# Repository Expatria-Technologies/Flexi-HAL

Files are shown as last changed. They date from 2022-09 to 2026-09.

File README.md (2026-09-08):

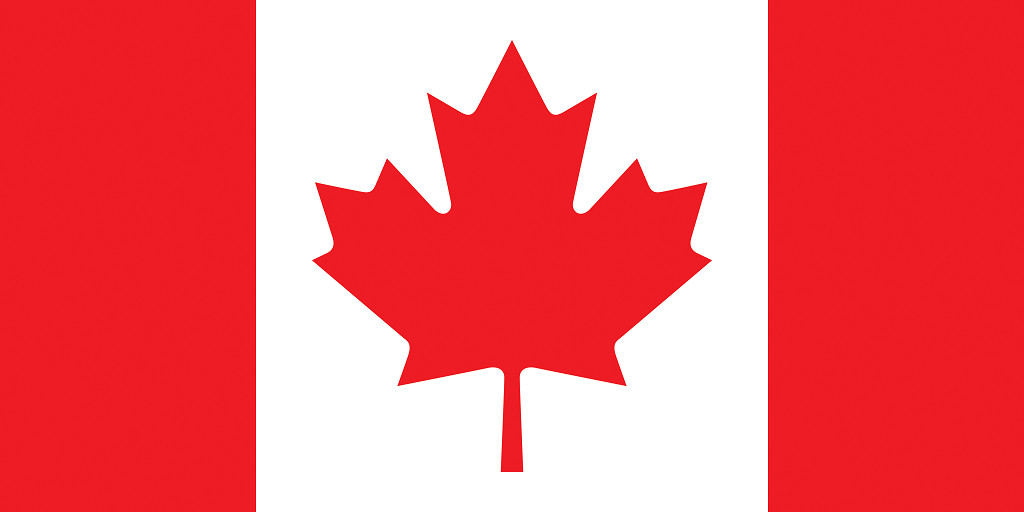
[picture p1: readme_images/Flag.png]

### Canadian-designed open source hardware. For everyone.

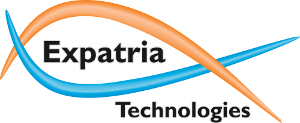
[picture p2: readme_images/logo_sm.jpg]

# Flexi-HAL CNC Controller
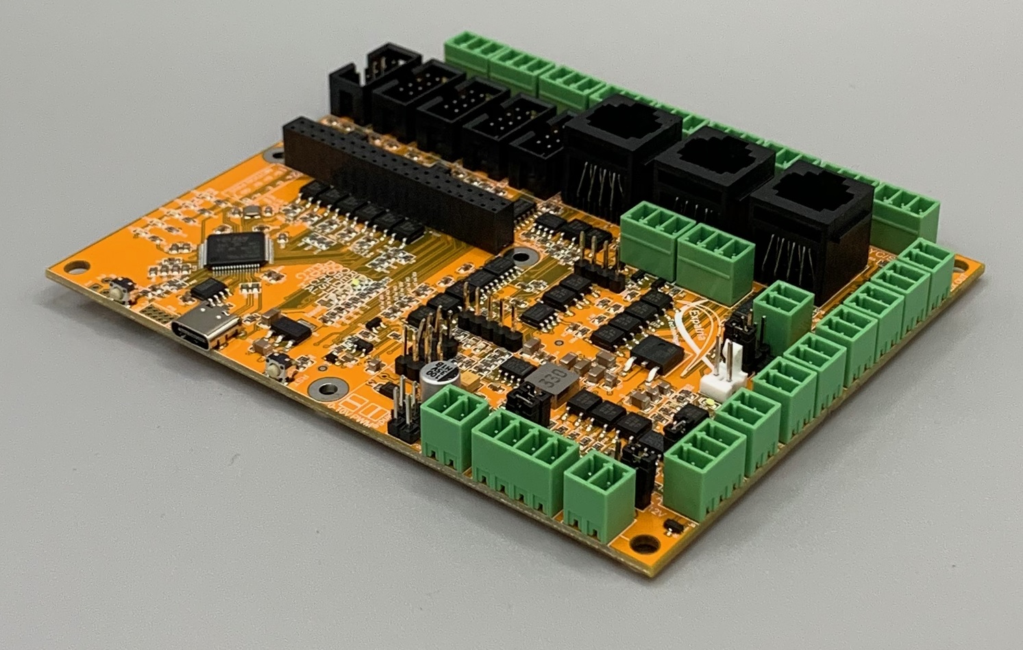
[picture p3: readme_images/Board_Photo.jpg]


Expatria Technologies GRBLHAL and LinuxCNC (and more!) CNC control board

Currently available in our online store:

https://expatria.myshopify.com/products/flexi-hal

Please consider buying a board to support our open-source designs. 

The Flexi-HAL was designed to be an EMI resistant IO platform for any microcontroller based CNC/motion control firmware or software.  This board includes a few features that we couldn't find on other boards, and it reduces the amount of extra wiring in our setups.  In the co-operative spirit of the PrintNC and other CNC communities, and Open Source Hardware, the Flexi-HAL will be licensed and free to use by all parties, including commercial parties, under the CERN-OHL-S V2 license.  It is our hope that the community finds the design useful and that it may be carried forward to help advance the PrintNC and broader CNC hobby community.

The Flexi-HAL incorporates community driven elements from the PrintNC Electronic Standardization (EST) Project.  As part of this project, two additional breakout boards have been created for the user controls and limits/probe inputs.  These are simple boards and could easily be milled and hand assembled, but fabrication files for each are available in the CAM_Outputs folder.  The inputs are accessible via the RJ45 connectors on the Flexi-HAL mainboard.  In addition, the Flexi-HAL is intended to be used with the Expatria Real-Time jog controller or similar peripheral:

https://github.com/Expatria-Technologies/RT_Jog_Controller

The key features of the Flexi-HAL:

1) 5 Axis of isolated step/dir motor control featuring high-speed digital isolators and differential signal drivers for maximum signal integrity and step rates.
2) Integrated support for 3 wire inductive type powered switches.
3) Onboard 5V power regulator.
4) Integrated RS485 with automatic direction control.
5) Support for closed loop stepper motors and servos with alarm feedback.
6) Differential interface for a spindle encoder inputC.
7) Real-time control port for remote handwheels and pendants.
8) Raspberry Pi GPIO connector allows integration of sender software and allows the board to host a full LinuxCNC installation.
9) 10V or 5V spindle control including PWM output via selectable jumpers.
10) 3 wire (powered) connections for standard CNC buttons on a breakout RJ45 connector that utilizes components compatible with the PrintNC EST project.
11) XYZA limit switches and probe/toolsetter on breakout RJ45 connector.
12) Flood/Mist/Spindle relay drivers.
13) Additional auxilliary inputs and relay driver outputs.
14) All machine facing IO is galvanically isolated from the MCU and user interfaces.
15) Easy reliable USB-C connection to a PC
16) GRBLHAL Ethernet Websockets or Telnet communication options with uFlexiNET module.
17) GRBLHAL SD card G-Code streaming and macro/subroutine storage (including looping and conditional execution) with uFelxiNET module.

Pre-compiled GRBLHAL binaries from are located here:  
https://github.com/Expatria-Technologies/STM32F4xx/releases

Source code for the customized Remora component to run in LinuxCNC is located here:  
https://github.com/Expatria-Technologies/remora-flexi-hal

Prebuilt Raspberry Pi 4B image is located here:  
https://github.com/Expatria-Technologies/Flexi-Pi

Accessory Breakout PCBs are located here:  
https://github.com/Expatria-Technologies/EST_Accessory_PCB

Various community mods and accessories are located here:  
https://github.com/Expatria-Technologies/Mods-Accessories

Recommended GRBLHAL Post Processor is here:  
https://github.com/Dietz0r/grblHAL_Fusion360_Post_Processor

uFlexiNET expansion card is here:  
https://github.com/Expatria-Technologies/uFlexiNET

The uf2 bootloader can be found here:  
https://github.com/Expatria-Technologies/tinyuf2/releases

## Flexi-HAL Overview

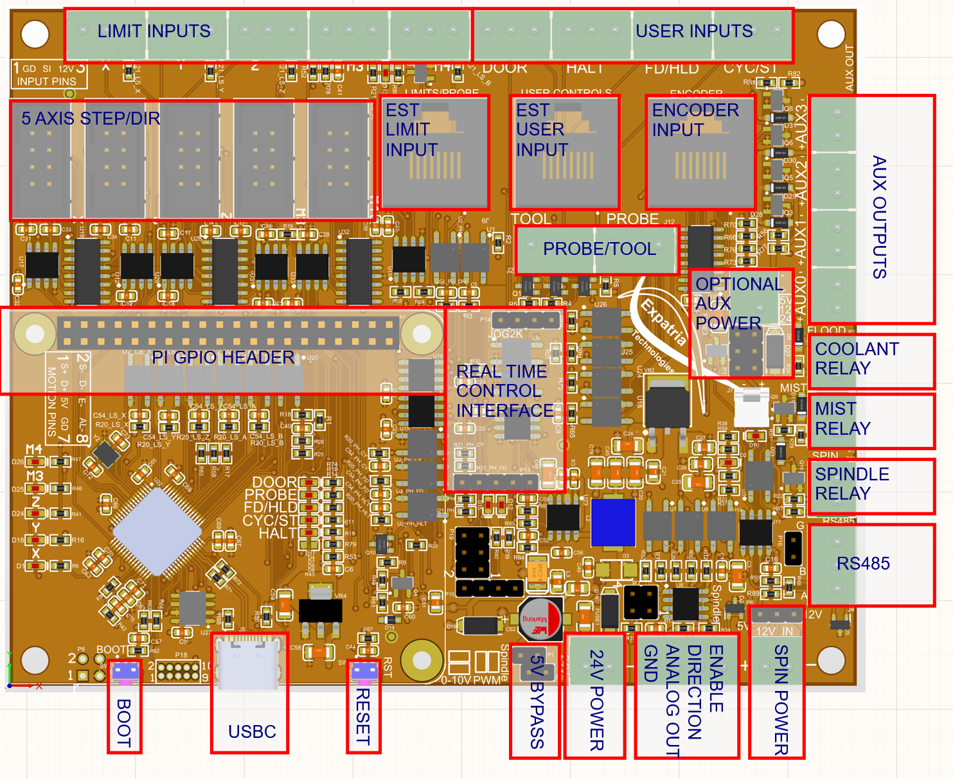
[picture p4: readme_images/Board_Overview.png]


Bottom side pin labels:

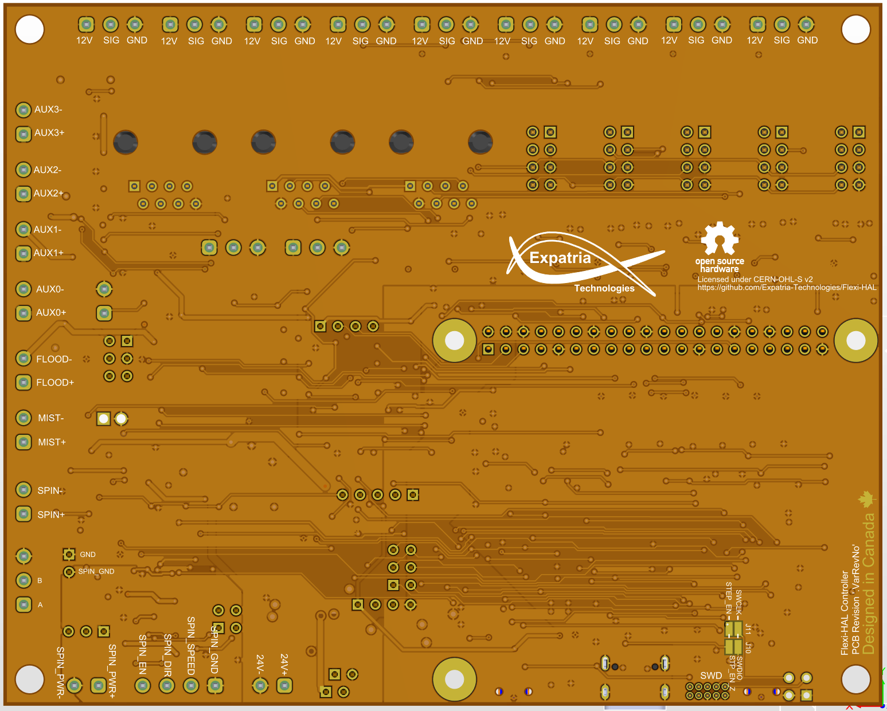
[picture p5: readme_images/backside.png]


Pinout List:

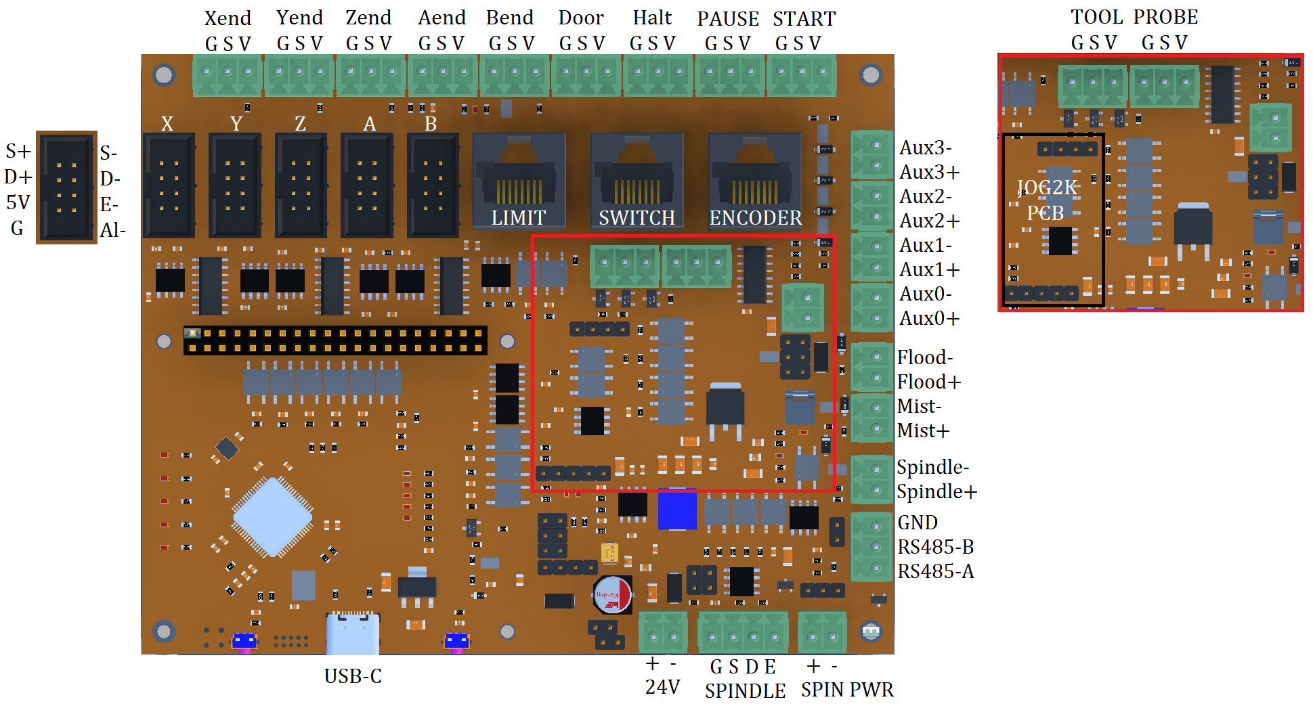
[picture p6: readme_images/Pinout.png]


### STM32F446 Microcontroller

Primarily, the board supports both GRBLHAL and LinuxCNC.  Binary firmware builds for different axis configurations are published on the Expatria Github.  In addition, a customized port of the awesome Remora project has been developed alongside Flexi-HAL so that you can easily switch to LinuxCNC.  With LinuxCNC, a Raspberry Pi 4b is installed in the Pi GPIO header to ensure the best possible signal integrity for the SPI step generation interface.

By using a common STM32F4 MCU, the Flexi-HAL is also able to easily host ports of uCNC, Marlin and even Klipper so it can drive much more than just CNC machines.

### UF2 Bootloader
The Flexi-HAL is meant to be used with a UF2 bootloader. All boards from Expatria will come with this bootloader installed. This allows you to upgrade or change the firmware on the flexi as easily as copying a file to a USB drive.  Pre-built binary firmwares from Expatria are distributed as UF2 files.  There are two ways to access bootloader mode and change the firmware:
1) Power up the MCU section (connect the USB cable) while holding the CYC/ST and FD/HLD buttons.
2) Double-tap the reset (RST) button on the side of the board near the USBC port.

Once in bootloader mode, the Flexi will appear as a USB storage device called "FLEXI446" and the X limit light will flash briefly if there is no signal asserted on that pin (switch is open).  Simply copy the new firwmare to this USB drive and the board will automatically install it and reboot.  Some operating systems may give an error when flashing is complete because the 'disk' was removed without ejecting it.  This error can be ignored.

### Power Input
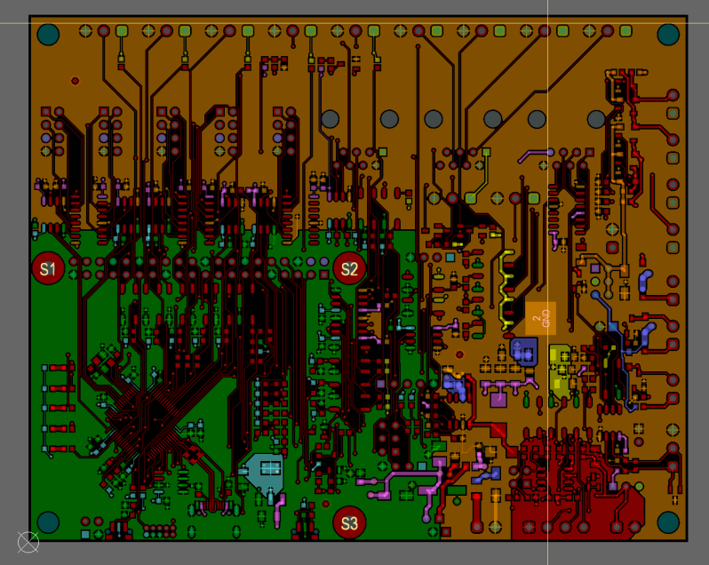
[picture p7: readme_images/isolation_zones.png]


The Flexi-HAL features the capability for full power and ground isolation between the sensitive microncontroller and host circuits, and the external IO that extends out to the rest of the machine.  There is a single input for 12-24VDC.  The board has its own onboard 5V regulator to power the stepper drivers and external RS485 interface.  There is also a small capacity 12V LDO that is specifically for driving the limit and user switches, as well as optionally providing the base voltage for the 10V spindle output.

Flexi-HAL has reverse polarity as well as over-current protection beyond 1A.  This is important to consider when using external relays that draw a lot of current as this may overwhelm the capacity of the board.  If you need to drive more than 250 mA through the auxillary and mist/coolant relay outputs, external relays are likely required.

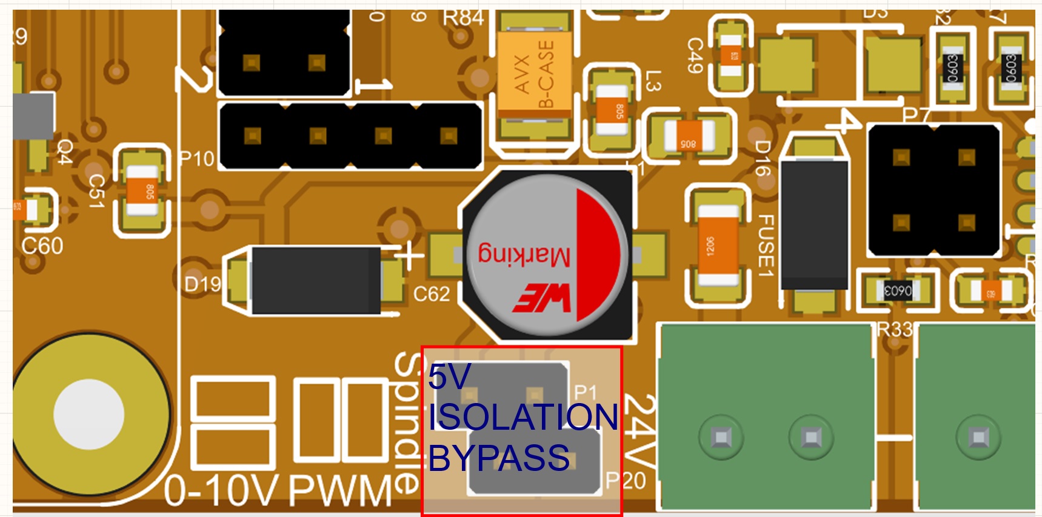
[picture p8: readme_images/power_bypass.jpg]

Normally the MCU and RPI header will be powered via the USBC connector.  The Jog2K is also powered from the isolated domain.  By installing two jumpers on the above offset pins, the 5V power and ground isolation can be bypassed and the Flexi-HAL will operate without an external 5V supply in a semi-isolated state.  This does reduce the EMI resistance of the board and is not recommended when sending Gcode via the USBC connector.

Note: With the isolation jumpers not-populatd, and the Flexi-HAL connected to 12-24v power, it may appear that the board is ready to run as some LEDs illuminate. You MUST provide 5v power to the isolated domain (MCU, Jogger) either through USB or the bypass jumpers in order for the MCU and Jogger to turn on!

### Stepper Drivers
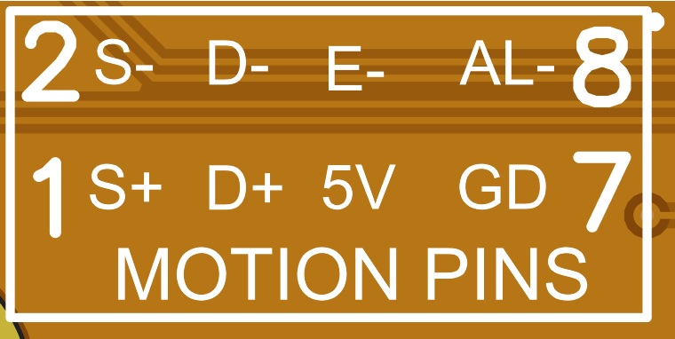
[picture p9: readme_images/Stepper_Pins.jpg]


The stepper drivers are designed to be used with IDC connectors that are quick to assemble.  Unfortunately you will need to ensure that at the external driver the high and low signal pairs are connected correctly as there is no standard pinout on these drivers.  The 8 pin connection allows you to run a high and low pair for every signal to ensure the best possible signal integrity.  The Flexi-HAL uses high speed digital isolators and differential RS-422 style signal drivers for the motion signals.

When using the alarm input the external drivers need to be configured for open-drain, active-low output.  The alarm output must be high impedance during normal operation.  In normal operation the blue MOTOR LED will be lit indicating that there are no active alarms.

Typical wiring for most open-loop stepper drivers: 



### Analog Spindle Control

Traditional GRBL spindle control interface for 0-10V or 0-5V spindle control.  Uses a dual-stage output driver for linear response.  Spindle power supply is selectable between 5V, 12V or external.  Note that when running the board with less than 14v input, it may not be possible to reach the full 10V output level - this is due to the dropout of the 12V LDO.  In this case, use the external spindle power input to connect your 12v and bypass the LDO for the spindle control voltage.

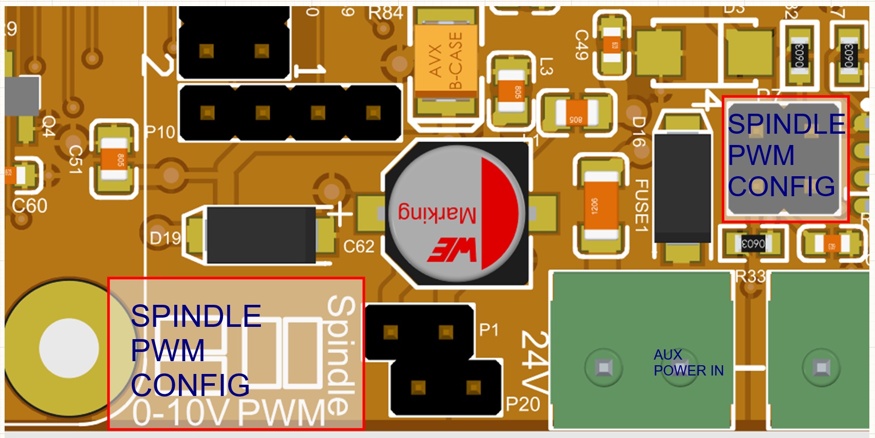
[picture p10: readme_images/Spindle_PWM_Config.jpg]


Near the main power input of the Flexi-HAL there is a diagram showing how a set of jumpers may be configured to enable 0-10V analog or TTL PWM output.  This jumper allows you to have a 12V compliant TTL PWM signal to drive a device like a laser engraver or an ESC.

Two headers - 3 pin P6 and 2 pin P16, connect the analog spindle section to the rest of the board.  P6 allows you to power the spindle section from either the onboard 5V or 12V rails.  If you remove P6 and P16 then the spindle section is completely isolated from the rest of the system and in this configuration can be used to drive motor controllers that require a floating control voltage.  Also, when driving the board with less than 14V input, it may not be possible to adjust the spindle output voltage to the full 10V.  In this case we recommend removing P6 (leave P16 in place) and applying 12V to the external spindle supply input directly.

### RS485 Spindle Control
This interface is primarily intended to be used with a Huanyang style VFD for spindle control.  The A, B and G (common) pins are marked on the top and bottoms sides of the PCB.  Simply connect the appropriate pins to the terminals on the VFD.  Note that the G pin should be used for signal common, it should not be connected to the shield of a shielded cable.

https://github.com/grblHAL/Plugins_spindle/

### 5 Axis limit inputs

By default both GRBL and the Flexi-HAL expect NPN NC limit switches.  PNP switches are not supported. NO switches can also be used on any switch input.

The first four axes have single limit inputs that are also accessible via the RJ45 EST limit breakout connector.  GRBL always knows the direction of travel so individual min and max pins are not required.  Auto-squaring is supported by enabling ganged axes in GRBLHAL and setting the appropriate pins.

In addition to the limit signals, there are two probe input pins on the limit RJ45 breakout connector and the main PCB that are multiplexed via XOR logic and share a single input pin on the microcontroller.

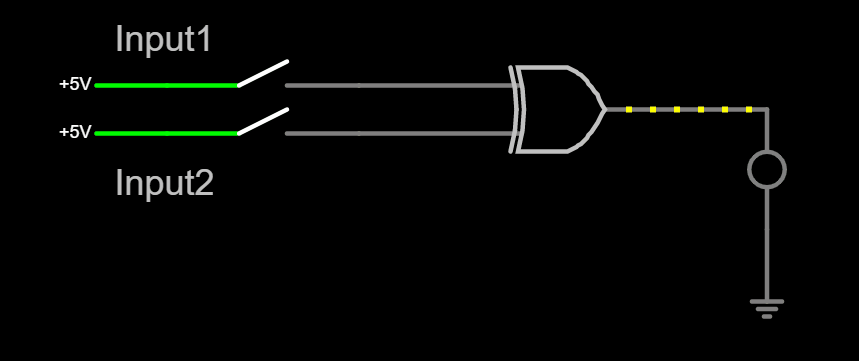
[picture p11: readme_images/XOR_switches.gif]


For the dual-input signals there is no need to terminate unused ports.

The RJ45 pinout:

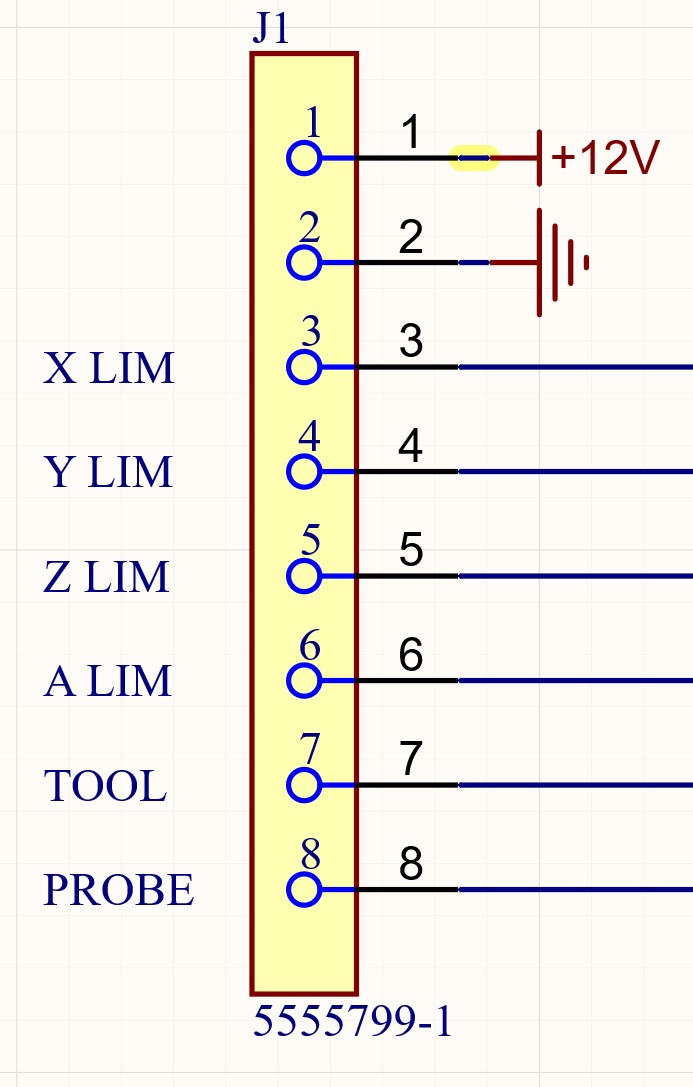
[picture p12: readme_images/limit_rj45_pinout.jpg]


### User Buttons

Standard CNC functions are mapped to 4 inputs.  These signals are primarily intended to be used via the user RJ45 connector.  They are also exposed via 3 wire connections on the main PCB.  These inputs have the same circuitry as the limit inputs and are NPN.  Connect SIG and GND to assert the signal.  When multiplexed these signals must be NO logic.

The RJ45 pinout:

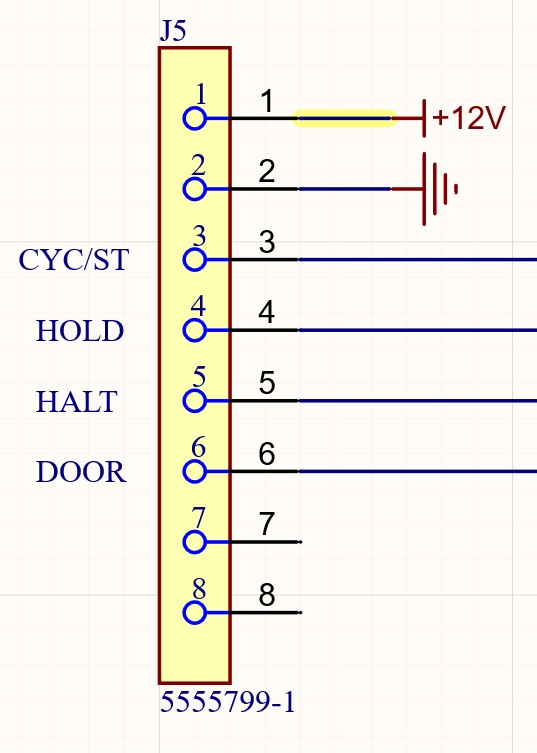
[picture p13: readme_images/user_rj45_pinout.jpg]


The HALT signal is not a safety feature and should not be used in place of a true electrical emergency stop.  It is intended to notify the controller of urgent requests and should be NO as it is shared between the PCB terminal block, RJ45 output and motor alarm.

### HALT Polarity Selection

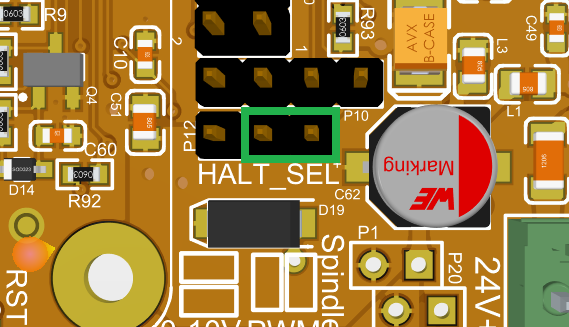
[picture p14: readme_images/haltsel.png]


Starting from A5 revision, the HALT signals from the Flexi-HAL board header port and the RJ45 user button breakout port are connected via an XOR gate. 
This was added to allow mixing "Normally Closed" (NC) and "Normally Open" (NO) switches.

At the default jumper position (illustrated above), Halt is triggered if the two ports have __different__ signals (High vs Low).
This means that a single NO, 2 NO, or 2 NC switches can be used.

| | Engaged Switch | Other Switch |
|---|---|---|
|Single NO | High | Low (Unconnected)|
|Two NO | High | Low |
|Two NC | Low | High |

If you wish to mix NO and NC, you need to move the jumper. Then Halt triggers if the two ports have __same__ signals.
Examples of this is using both the User Button Breakout (NO) and the common Toolsetter with overtravel protection (NC).
| | Halt button (NO)| Toolsetter overtravel (NC)|
|---|---|---|
|Halt pushed | High | High |
|Toolsetter pushed| Low | Low |

If you are in doubt of the correct header position for your case, you may simply try both positions and choose the one where the HALT signal is not asserted (red light is not on) when in the nominal operating condition.

(__Note:__ Do not change GRBL setting 14 to try and invert the halt("EStop"), as this is not the same and can make the Jog2K Halt button unresponsive)

### Spindle, Flood and Mist relay drivers
The Spindle, Flood and Mist relay outputs are driven from the main board supply.  External relays should be selected to match the power supplied to the Flexi-HAL.  The absolute maximum coil current for each output should not exceed 250mA.  In general, the coil resistance should be 150 Ohm or greater.  The relay outputs are active-low, the high side is connected to the main power input.

### Auxillary relay drivers
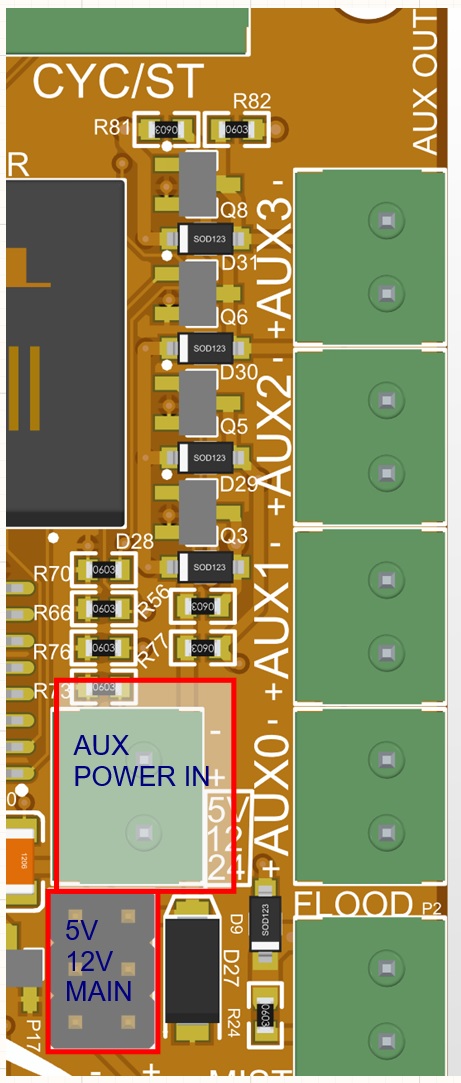
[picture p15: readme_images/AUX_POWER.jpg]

Four axilliary relay outputs are exposed.  These have a maximum combined drive current of 1000 mA when operated via a dedicated power supply.  The relay voltage can be selected via a 3 pin jumper between the main board power supply, the onboard 12V supply and the onboard 5V supply.  If the jumper is left unpopulated power for the aux outputs is supplied via the dedicated (fused and polarity protected) input.  The 12V and 5V options cannot drive more than 20 mA per pin and are only used for TTL signalling applications - they should never be used to drive inductive loads.  Never populate P17 and the external supply at the same time.  When driving external relays, the coil resistance should be 150 Ohm or greater.  The relay outputs are active-low, the high side is connected via the power selection jumper.

### Real-Time Control Port
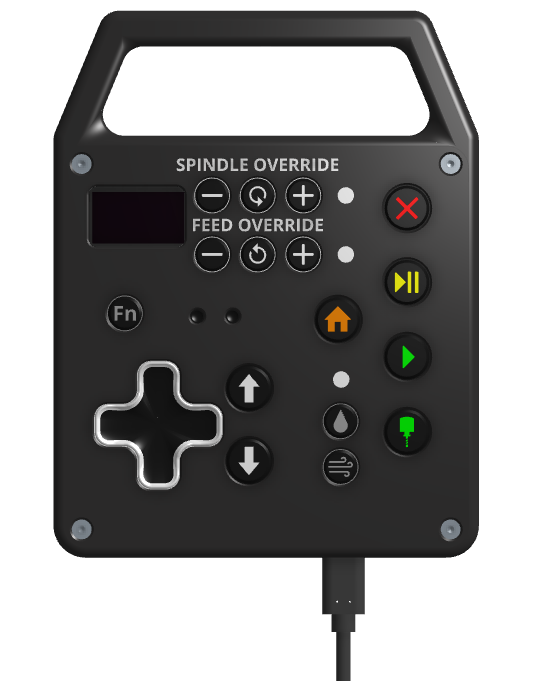
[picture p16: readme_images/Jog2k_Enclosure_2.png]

This port is intended to allow for external pendant type devices to issue real-time jogging and override controls to the motion  controller.  It uses I2C signalling and adds additional signals for the keypad interrupt as well as the Halt signal.  We feel that a robust and wired control is the safest way to interact with a CNC machine in real time.  A simple reference controller implementation is under active development, but there are some code examples referenced in the GRBLHAL I2C keypad plugin repository:

https://github.com/grblHAL/Plugin_I2C_keypad/

https://github.com/Expatria-Technologies/RT_Jog_Controller/

### Spindle Sync Port
This port allows a differential connection to an external module for a robust GRBLHAL lathe implementation or to support a high-speed encoder input for LinuxCNC.  An encoder such as E6B2-CWZ1X is suitable for most spindle applications.

There is also a small breakout available that exposes these signals for 5V single-ended NPN input to interface with more basic sensors and other switched inputs.

The RJ45 pinout:

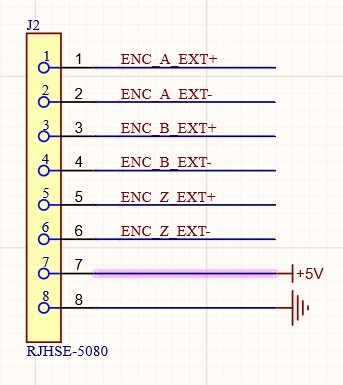
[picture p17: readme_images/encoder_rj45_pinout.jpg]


### Raspberry PI expansion header
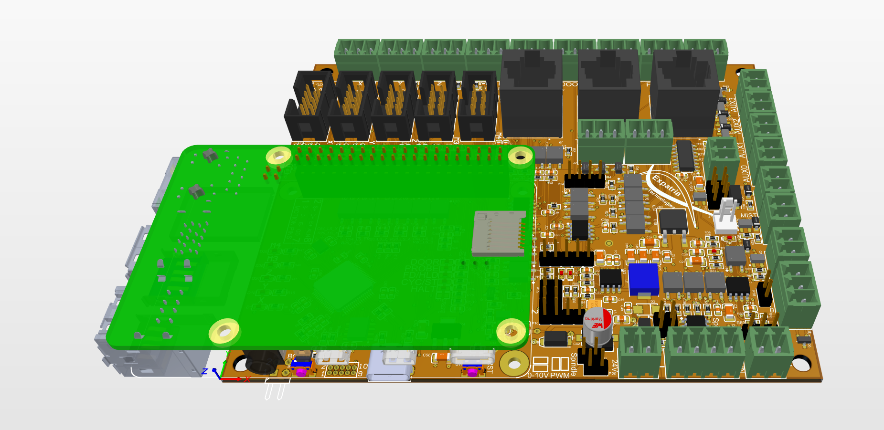
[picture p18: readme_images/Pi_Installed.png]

The Rasberry Pi GPIO header allows the Flexi-HAL to host a full Raspberry Pi type SBC.  This allows the platform to support LinuxCNC via the Remora project.

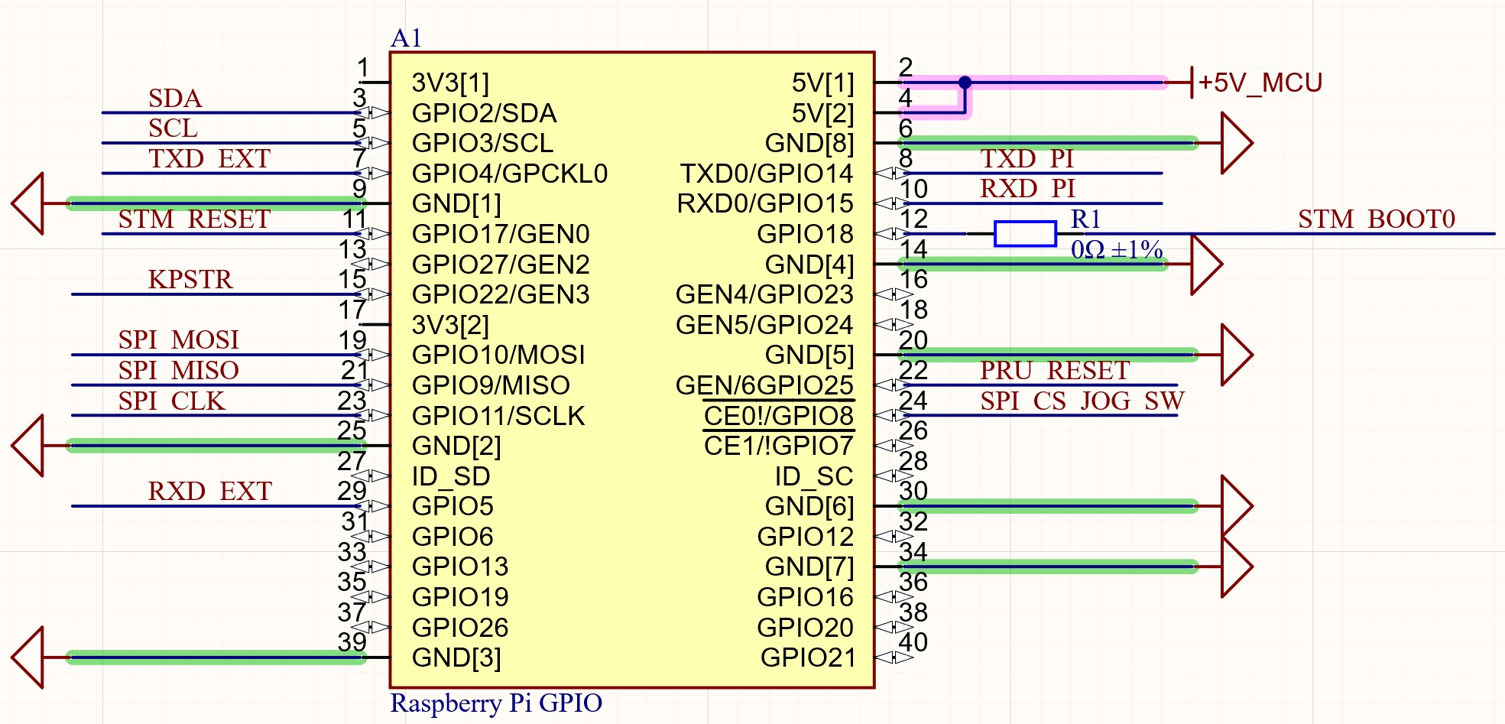
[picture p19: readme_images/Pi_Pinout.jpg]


### Accessories
Some 3D printed accessories are avilable in [Mods & Accessories](https://github.com/Expatria-Technologies/Mods-Accessories/), including a DIN rail mount and enclosures/mounts for the limit and button breakouts.

### Default Jumper Locations

By default the following jumpers (shown in the graphic in RED) should be populated.
This has the following effects:
The RPI Header uart is connected to the internal MCU UART - this is necessary to flash Remora firmware from the RPI and also is used with the uFlexiNET module for the SD card chip select.
The HALT polarity is set for use with an NO button like the button breakout.
The analog spindle output is set for 0-10V.
The analog spindle section is connected to the onboard 12V supply.
The analog spindle section ground is connected to the PCB external ground.
The aux outputs are powered via the main 24V input.

### Example Wiring Diagram
A comprehensive wiring diagram has been developed by the PrintNC community using the FlexiHAL.  While not specific to Flexi, this gives a great example of how to connect the board into the rest of a complete electronics box to drive a CNC machine. 
https://wiki.printnc.info/en/v3/wiring

### Attributions
This project uses components from the very helpful actiBMS library.

https://github.com/actiBMS/JLCSMT_LIB

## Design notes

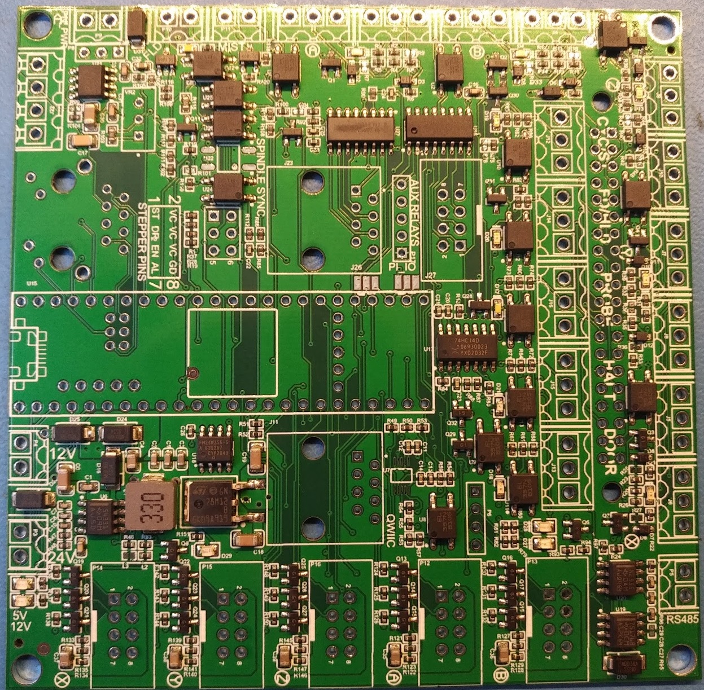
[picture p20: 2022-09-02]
readme_images/EarlyBoardPhoto.jpg

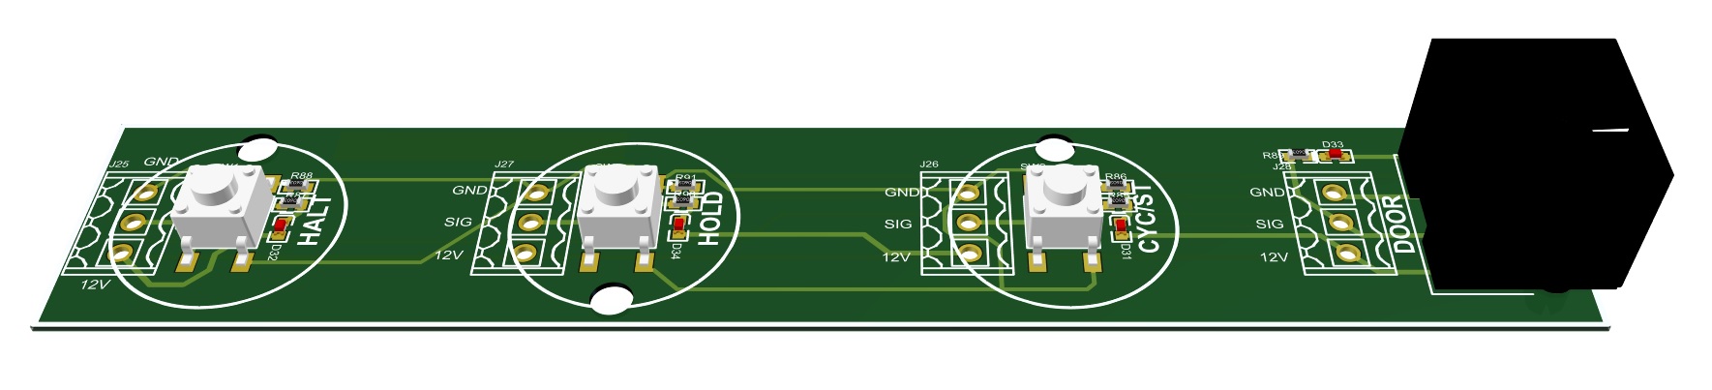
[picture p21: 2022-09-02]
readme_images/User_mod_render.jpg

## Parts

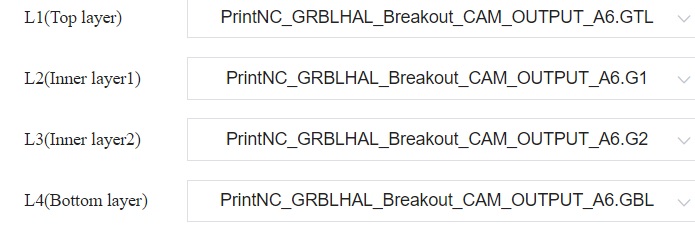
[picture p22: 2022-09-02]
readme_images/Hal2k_Layer_order.jpg

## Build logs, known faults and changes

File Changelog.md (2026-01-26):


# Flexi-HAL CNC Controller

## Changelog

### A4 Revision

- Initial Release

### A5 Revision
- Added HALT signal polarity selection.
- Modified RS485 UART isolation for better compatibility with more VFDs under LinuxCNC.
- Added jumper resistor option to route STP_ALARM signal to B limit switch input.
- Depopoulated isolation bypass headers to prevent magic smoke escape.
- Added termination resistors to encoder input to improve signal integrity.
- Added additional overvoltage protection to external circuits.

- ### A7 Revision
- Fixed silkscreen issue on Probe and Tool ports.
- Updated silkscreen to clarify copyright permissions on Expatria and FlexiHAL names.
- Added solder points to USB nets on top layer.
- Changed encoder routing for better signal integrity.

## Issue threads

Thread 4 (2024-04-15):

Dual x axis request

aaronblue1, 2024-04-15:
Hi,

I need a configuration with dual x axis and probe.

andrewmarles, 2024-04-15:
To be clear, you re looking for dual X axis and single Y axis?  There is a ganged X, ganged Y config there (used by mpcnc style machines).

https://github.com/Expatria-Technologies/STM32F4xx/releases/download/flexi-hal-v0.9.9.8/FLEXI_HAL_XGANG_YGANG_ETH_SD_PRB_20231229_180124.1.uf2

aaronblue1, 2024-04-15:
Hi yes, I'm looking for dual or ganged x axis and a single y axis. I'm converting an old multicam atc machine.

Aaron

andrewmarles, 2024-04-15:
Builds is added here:

https://github.com/Expatria-Technologies/STM32F4xx/releases/download/flexi-hal-v1.0.0.0/FLEXI_HAL_XGANG_ETH_SD_PRB_20240408_140424.uf2

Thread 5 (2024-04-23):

How to reset onboard settings.

hambudi, 2024-04-23:
I started using FlexiHal board to CNC my sherline mill. For some reason my X axis stopped moving yesterday while I was testing things (upgrading firmware etc). The issue seems to be with the board/firmware, because if I switch X with Y it works fine.

How do I reset the board to default firmware and settings?

andrewmarles, 2024-04-24:
`$RST=$` is the command to reset the GRBL settings.

This is the release that is currently shipping on the boards:
https://github.com/Expatria-Technologies/STM32F4xx/releases/tag/flexi-hal-v0.9.9.8

hambudi, 2024-04-24:
ok, I tried flashing the 9.9.8 firmware, I tried resetting the board. Looks like somehow my x axis is broken on this board.

For now I am able to use the beta firmware with the ganged X axis to get my machine to work (By hooking up the X stepper to A). Hooking up a scope to the x axis output shows that its not outputting anything.

Any hints about how this could have happened? My board is connected to a bunch of CL-57T Closed Loop drivers running my CNC. The board is powered by a 20v laptop power adapter, and the usb cable for 5v.

andrewmarles, 2024-04-24:
ESD is always a risk with any electronics.  There are protection devices on the board but there are not 100% proof against damage from handling.

hambudi, 2024-04-24:
Photos below.

Black box has an unregulated 50V power supply powering the stepper drivers. Flexi was screwed to 3d printed DIN Bracket and sticky taped to the top of black box.

Only wires from flexi to black box are stepper wires, limit wires go using ethernet cable directly to the CNC.

Flexi has USB and 20V DC connected as well.

Photos below show jog controller connected, this was not connected when the issue started happening.

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

andrewmarles, 2024-04-24:
You may want to check the grounding on the stepper drivers to ensure that there is no ground loop between your 50V supply and where the PCB external gnd is connected.  There's really no definitive answer I can give you from over here, but yoru wiring looks in the pictures.  In terms of specific failure point, as your Y axis is working the likely victim here is U17, the x-axis step/dir isolator which is at the edge of the board near the RPI header and stepper connector.

hambudi, 2024-04-24:
In the attached photo that little chip does look pretty mangled.

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

I dont understand ground loops very well, but everything in the 50V line is grounded correctly based on all the info I could find based on stepper driver wiring documentation. The only ground connection between the board and the 50V line is probably through the power strip they share, and then through the computer, through the USB port.

When I hooked up a scope to the board to see how the stepper outputs were, there was a lot of noise/ripple when not operating steppers. It cleaned up when i ran the axis. Is this indication of a ground loop?

Should I be grounding the CNC board to the stepper 50V supply more directly to avoid loops?

hambudi, 2024-04-25:
Thanks

Closed 2024-04-25.

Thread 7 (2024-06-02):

Using a controller with a burnt out X axis opto.

hambudi, 2024-06-02:
Hi, in a previous issue we determined that my board's X axis opto isolator was blown. I have been attempting to use this board using ganged x ganged y firmware. And plugging in the X axis stepper into M3.

I have a rather weird issue with this setup where if I configure my X to job correctly from the computer, the Jog2K pendant moves it in the opposite direction. I never had this issue before I used the ganged firmware.

1- I'm wondering if its possible for you to provide me a firmware where the X axis is configured to output on the M3 slot without any ganging.

2 I'd like to replace the blown opto but dont know what the part is to replace it with. Can you please link me the part number of specs so I can find an equivalent?

hambudi, 2024-06-02:
This is the blown opto in question https://github.com/Expatria-Technologies/Flexi-HAL/issues/5#issuecomment-2076066670

andrewmarles, 2024-06-02:
This is the part on the board:
https://www.lcsc.com/product-detail/Digital-Isolators_Corebai-Microelectronics-CBMuD1200LAS8_C476470.html

This is an equivalent from digikey:
https://www.digikey.ca/en/products/detail/analog-devices-inc/ADUM1200ARZ-RL7/995653

The source tree is here (linked from the readme) for the driver is here:
https://github.com/Expatria-Technologies/STM32F4xx

You just need to clone it and change the flexi_hal_map.h file for your desired pinout:
https://github.com/Expatria-Technologies/STM32F4xx/blob/F446_Flexi_HAL/boards/flexi_hal_map.h

hambudi, 2024-06-02:
Thank you!

Closed 2024-06-02.

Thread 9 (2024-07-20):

Flexihal PrintNC Without RGB

rcrules, 2024-07-20:
Would it be possible to make a PrintNC release without "STATUS_LIGHT_ENABLE=1", so all of the Aux pins are available for use?  Something like FLEXI_HAL_PRINTNC_NORGB_20240604_060724.uf2 or similar?  Thank You!!

andrewmarles, 2024-07-22:
This build is what you describe:
https://github.com/Expatria-Technologies/STM32F4xx/releases/download/flexi-hal-v0.9.9.8/FLEXI_HAL_YGANG_ETH_SD_PRB_20231229_180124.1.uf2

rcrules, 2024-07-22:
Thanks for the reply Andrew!!!

I have seen this request mentioned several times on the Discord, as of late.  I did try "FLEXI_HAL_YGANG_ETH_SD_PRB " after I saw it mentioned on the Discord, but I got some errors when restoring a setting.txt file, in IOSENDER, about incompatible features.

Also, according to the Build Configurations the "FLEXI_HAL_YGANG_ETH_SD_PRB" file doesn't contain SAFETY_DOOR_ENABLE=1.

Thanks again for the consideration!!

Closed 2024-07-22.

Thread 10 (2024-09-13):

Raspberry Pi and communication with Flexi-HAL

drpixel8, 2024-09-13:
If I am understanding the README correctly, I should be able to run cnc.js on a Raspberry Pi that is attached to the GPIO header and communicate with Flexi-HAL. Is this accurate?

After following the installation guide listed on the [cnc.js website](https://cnc.js.org/docs/rpi-setup-guide/) and after enabling the serial port using `sudo raspi-config`, I am able to see an available port when running cnc.js, however, when I connect to it, I see no output when issuing GRBL commands.

I've tried searching, but have found nothing that states what pins the Flexi-HAL uses to communicate with the Raspberry Pi.  I am assuming it uses GPIO14 & GPIO15, which would correlate to UART1 on the Raspberry Pi, correct?  If not, what UART/pins should I be using.  Does Flexi-HAL expect RTS/CTS flow control or any other settings?  I've tried several combinations, but nothing seems to be working out.

What driver should I be using with this?  Does a driver with Ethernet and/or SD alter the ability to communicate with the Raspberry Pi?

andrewmarles, 2024-09-13:
The schematic shows what pins connect where:
https://github.com/Expatria-Technologies/Flexi-HAL/blob/main/FLEXI_HAL_2000_Schematic_A5_FULL_PLACE.PDF

None of the pre-compiled builds have the UART enabled.  The builds for uFlexiNET repurpose one of the UART pins for an additional CS pin.  I would suggest just using a short jumper cable between your PI and the USB port.  Native USB-CDC is a faster and more robust communications interface than UART.

Closed 2024-10-04.

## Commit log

2022-08-03 Commit A4 Schematic PDF.
2022-09-09 Commit design files.
    [12V_Power_Supply.SchDoc, 2xparallelswitch.SchDoc, 5V_Power_Supply.SchDoc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]
2022-10-13 Commit board step file.
2022-10-13 Commit DIN mount.
    [DIN_Clip.stl, Flexi-HAL_Mount_Plate.stl]
2022-10-18 Commit mild schematic PDF fixes.
2022-11-29 Commit A4 build files.
    [FLEXI_HAL_2000_CAM_OUTPUT_A4.csv, FLEXI_HAL_2000_CAM_OUTPUT_A4.xlsx]
2023-01-22 Remove DIN mount, which has been migrated to Mods & Accessories
    [DIN_Clip.stl, Flexi-HAL_Mount_Plate.stl]
2023-04-26 Commit A5 revision files.
    [2xparallelswitch_HALT.SchDoc, 5V_Power_Supply.SchDoc, Aux_Outputs.SchDoc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]
2023-05-07 Updated isolator part number.
    [FLEXI_HAL_2000_CAM_OUTPUT_A4.xlsx]
2023-06-09 Commit A5 fabrication files.
    [FLEXI_HAL_2000_CAM_OUTPUT_A4.xlsx, FLEXI_HAL_2000_CAM_OUTPUT_A5.csv, FLEXI_HAL_2000_CAM_OUTPUT_A5.xlsx]
2023-09-29 Updated some component values.
    [FLEXI_HAL_2000_CAM_OUTPUT_A5.xlsx]
2024-06-09 Update README.md
    Added note on isolated power
2024-07-04 Commit latest PNP.
    [FLEXI_HAL_2000_CAM_OUTPUT_A5.csv]
2024-08-21 remove unused page.
    [12V_Power_Supply.SchDoc]
2024-10-04 Commit Updated A6 design files.
    [FLEXI_HAL_2000.PrjPCB, STM32F446RE_board.SchDoc, Spindle_Sync.SchDoc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]
2024-10-04 Commit A6 updates.
    [FLEXI_HAL_2000.PrjPCB, RS485.SchDoc, STM32F446RE_board.SchDoc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]
2024-10-04 Update index.
    [FLEXI_HAL_2000_CAM_OUTPUT_A5.csv, FLEXI_HAL_2000_CAM_OUTPUT_A5.xlsx]
2024-10-19 Commit schematic pdf.
2024-10-30 Commit A7 updates.
    [FLEXI_HAL_2000.PrjPCB, Spindle_Sync.SchDoc]
2025-03-04 commit cdn
    [FLEXI_HAL_2000.PrjPCB]
